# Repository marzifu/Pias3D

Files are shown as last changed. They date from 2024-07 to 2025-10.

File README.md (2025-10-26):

# The Problem
I've always wanted to make and/or source my own Voron and the likes. But the main problem I kept facing is the unimaginably expensive kits that are being sold here in Indonesia, or just the shipment cost + tax that doesn't make sense for me to pay.

Other than that the cost of basically the cheapest CoreXY is around $800 USD _my hopes and dreams_.

# The Solution?
I learnt how to use FreeCAD to draw up my hilariously bad designs until I came to this rendition of the machine which I called Pias. _fancy~_

But no, the name just suggest the eternal loop of fixing, upgrading, maintenance, and what not. Which is what I want to minimize by creating a "proper" machine.

So after scouring countless builds of 3D printers, anything from Rolohaun's build, Mikhail Design's build, and Voron's. I decided to find parts that is easily found here, and thus decided to design a machine around the parts that I find. With the main focus of:

### 1) Keeping It Affordable
The reason this is the main focus is because, good 3D printers are expensive— Even more so for CoreXY systems (Usually an additional $200-$300 _yikes_).

So with that I tried to find hardwares that are a good start, but could be upgraded along the way. Because the important part is for you (and me) as a hobbyist, to be able to build a machine.

### 2) Ease of Procurement
I know this is different to everyone, but my main goal for now is to make a machine that could easily be built by anyone with what we have (Importing's out of the question for us, _unless you have a wae_, in which I dont).

Though there are some Mellow parts that are being sold, the parts are almost 5x of some generic ones. You can get those parts sure, but for the sake of keeping my wallet not empty I am crossing that.

### 3) Upgrade and Update
My first experience with troubleshooting a printer is with a Kingroon KP3S Pro V2, which wasn't fun. I had to replace the mainboard two times, and then ended up switching to a BTT board which is going great.

Tinkering is not fun, if its undocumented and you can reach no one. With that the plan is to document every single upgrades, and update this repository for future builds. It could be some loose fits, or even some arbitrary auxiliary stuff, but documentations are crucial for the longevity of this project.

# Changelogs
### 04/25/2025
Finally back to maintaining this repository after I actually finished the 4th? 6th? rendition of this project. The basic idea of selling it is still in mind, but right not he focus is to have a proper prototype build that could work to print virtually any "normal" material eg. PETG, ABS, ASA, TPU.

I'll try to make a comprehensive build guide, but I do not know how to make a guide like how Voron/Annex which is what I strive for. It's going to be scuffed, but please bear with me.

The next update on this log would probably be an update by creating BOM and pricing in IDR (Indonesian Rupiah), and then converting it to dollars and then saving the links somewhere.
Cheers to this project!

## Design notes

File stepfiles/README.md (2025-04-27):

# A Slight Warning
The designs I have are rough. I have no actual experience in any CAD designs.

I find some parts have a slightly cursed geometry or slices, and that is because that is the only idea I have to actually solve the problem at hand.
Please scrutinize my designs, and help me learn and improve in designing stuff.

Other than that please edit the files to your hearts content :)

# Overview
Attached is a (v1) overview
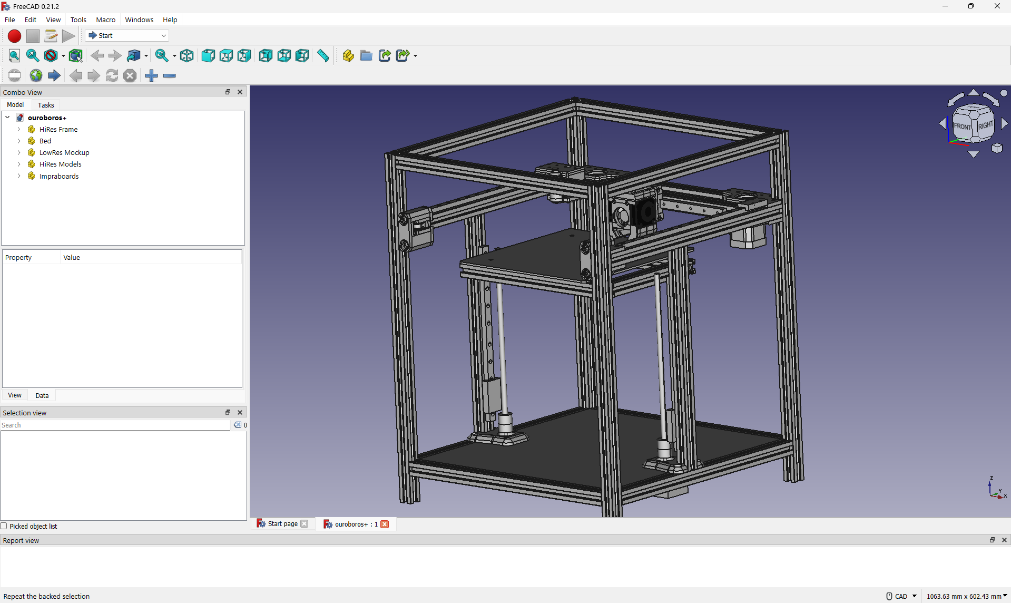
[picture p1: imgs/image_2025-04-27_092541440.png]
Overview


The picture and the 'version' tag will be continously updated with newer versions of the model.

The next goal is to have a rendered version to showcase here with different sections.

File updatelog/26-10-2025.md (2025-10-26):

# Sunday, 26-10-2025
### This log is meant as a way to log the problems that has came up, and my thoughts on the current problems.

Quick update on the current progress

The printer has been built, and is running, though there are some hiccups along the way.
A comprehensive list of BOM could already be made, but I will do that later after a redesign on the current Pias design.

The current plan is to start redesigning starting from the extruder unit, and move to the other parts from there.
I plan to keep the semi-organic-ish design (rarely hard edges), on most of the parts and improve parts that still have a lot of sharp edges.

The thing that I wanted to highlight on this redesign is that in the current rendition of the extruder unit is lackluster.
From the assembly process, and other issues like the management of the GT2 Belt and cables. The process is convoluted, and very tedious to do.
Especially if the goal is to assemble it flush, and close to no wobble.

The glaring issue is that the four contact point of the extruder units is in a weird place, that could be remedied quite easily.

The current plan is to make make the main extruder units (Hotend, Fans, and whatnot) to be separate from the extruder's carriage.
Meaning the main extruder and it's carriage would be separated to two different object if the four contact points were to be taken off.

### What do you even mean by that?

The current main extruder unit is built into three parts, Face, Front, and Back.  

**Face** is the biggest part, including the duct, and the place where the fans will be held.  
**Front** is the first half of the hotend holder, that is closer to the face part.  
**Back** is the second half of the hotend holder, that is closer to the extruder carriage.  

The assembly process for the whole thing is as such:  

1. Prepare the GT2 Belt, and all the cables from the 3 fans, hotend, and klicky.
2. Put the hotend in the Front and Back parts, while managing the belt and cables.
3. Put the assembled FB (Front - Back) unit, and screw the mounting points to the extruder carriage  
   again, mind the cable and belts.
4. If the cable and the belt are managed correctly, the FB unit should be flush with the carriage, if not. Then the belt or cable could be in between.
5. After the FB unit is correctly installed, then continue to prepare the addition of the Face unit.

The list doesn't really do the complexity justice, because the fans has to be placed in advance in the Face unit,
and the cables must have enough slack to not destroy the connection on the fans itself, but not too much so that the fans (especially the part cooling)
would not be tight in the fan places.

All this would make the face part dangle while you have to adjust the position of the GT2 Belt and still having to cable manage so that everything is in the correct place. _yikes_

Then the thought of writing what is wrong with the current edition came up.  
The main thing that I want to fix first is to do separate the two assembly, and then proceed to do a refinement on duct design, and some optimizing on the XY Carriage.

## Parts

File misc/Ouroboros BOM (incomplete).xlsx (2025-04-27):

Category | Item | Details | Quantity | Price | Sub-total | Total
Main Frame | 2020 T Slot | 50cm | 4 | Rp 25000.00 | Rp 100000.00 | Rp 2435810.00
 | 2020 T Slot | 36cm | 10 | Rp 18000.00 | Rp 180000.00
 | 2020 T Slot | 34cm | 1 | Rp 17000.00 | Rp 17000.00
 | 2020 T Slot | 32cm | 2 | Rp 16000.00 | Rp 32000.00
 | 2020 T Slot | 27cm | 2 | Rp 13500.00 | Rp 27000.00
 | 2020 T Slot | 24cm | 1 | Rp 12000.00 | Rp 12000.00
 | 2020 T Slot | 15cm | 2 | Rp 7500.00 | Rp 15000.00
Motion | Nema 17 | Hanpose 17HS4401S | 4 | Rp 95000.00 | Rp 380000.00
 | MGN9H + Rail | 300mm | 2 | Rp 200000.00 | Rp 400000.00
 | MGN12H + Rail | 300mm* | 3 | Rp 200000.00 | Rp 600000.00
 | T8x8 | 250mm | 2 | Rp 39000.00 | Rp 78000.00
 | POM Screw Nut |  | 2 | Rp 20000.00 | Rp 40000.00
 | Rigid Coupler | Generally D20 L25 | 2 | Rp 30000.00 | Rp 60000.00
 | GT2 Belt 6mm | 2 m | 1 | Rp 100000.00 | Rp 100000.00
 | GT2 20T 6W Pulley | 5mm bore | 2 | Rp 10000.00 | Rp 20000.00
 | GT2 20T 6W Toothed Idler | 5mm bore | 2 | Rp 13000.00 | Rp 26000.00
 | GT2 20T 6W Smooth Idler | 5mm bore | 10 | Rp 13000.00 | Rp 130000.00
Fasterner | M6 x 12 BHCS | Frame joints | 30 | Rp 1567.00 | Rp 47010.00
 | M4 x 12 Countersunk | Bed mounting | 4 | Rp 700.00 | Rp 2800.00
 | M5 x 10 BHCS | XYZ part mounting | 50 | Rp 800.00 | Rp 40000.00
 | M3 x 8 BHCS | Rails mounting | 50 | Rp 500.00 | Rp 25000.00
 | M4 Sliding T Nut | Bed mounting | 4 | Rp 1000.00 | Rp 4000.00
 | M3 Sliding T Nut | Rails mounting | 50 | Rp 1000.00 | Rp 50000.00
 | M5 Sliding T Nut | XYZ part mounting | 50 | Rp 1000.00 | Rp 50000.00

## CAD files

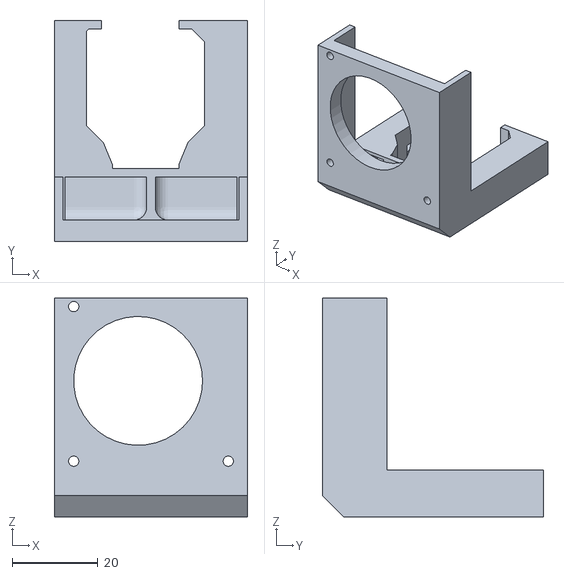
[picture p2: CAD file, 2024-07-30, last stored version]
STL/Part Cooling Duct.stl
45.0 x 51.5 x 51.0

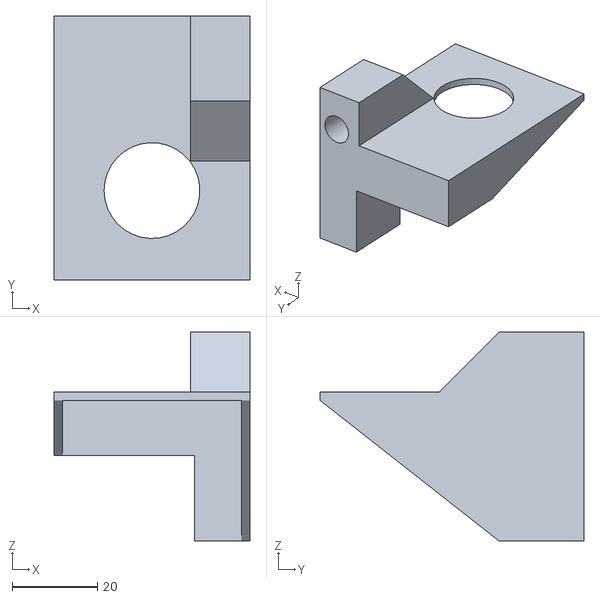
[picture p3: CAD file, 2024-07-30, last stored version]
STL/Right Motor Holder.stl
46.0 x 62.0 x 49.0

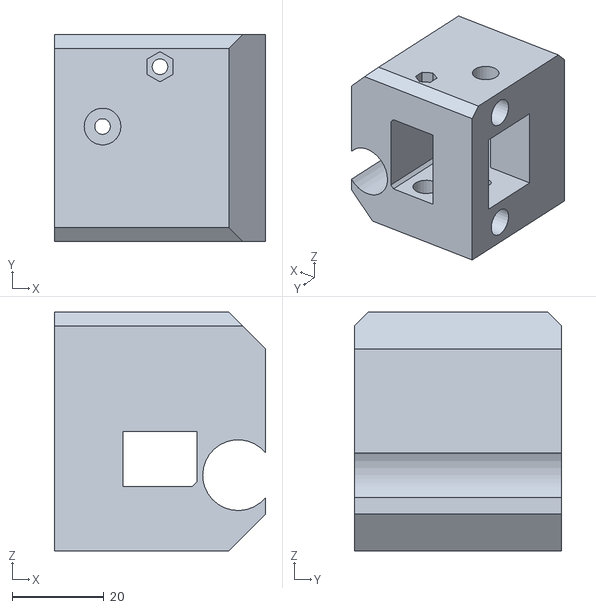
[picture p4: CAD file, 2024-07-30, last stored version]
STL/Right Gantry Holder.stl
46.0 x 45.0 x 52.0

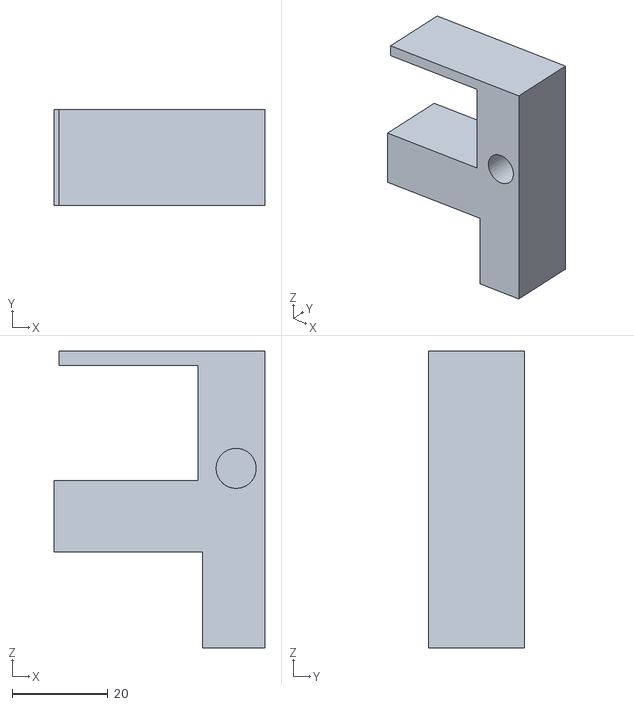
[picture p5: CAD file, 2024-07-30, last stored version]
STL/Right Idler.stl
44.0 x 20.0 x 62.0

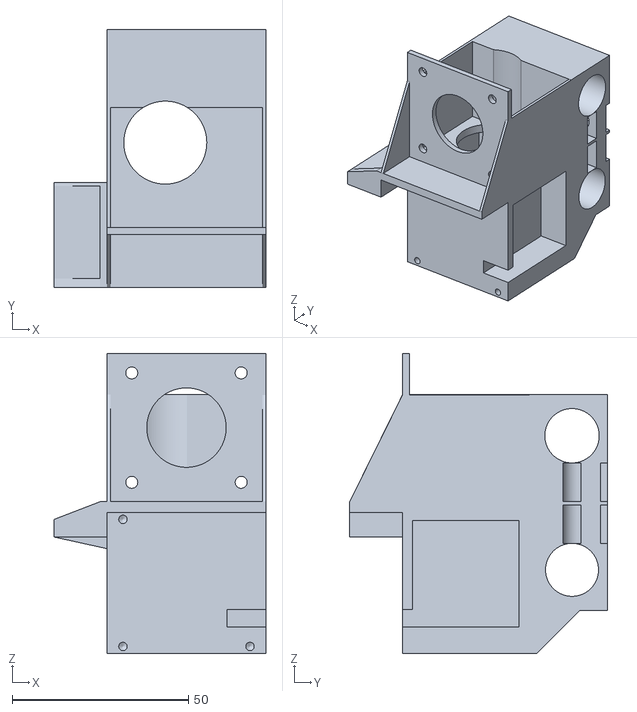
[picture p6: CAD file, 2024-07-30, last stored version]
STL/Carriage.stl
60.0 x 73.0 x 85.0

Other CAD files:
STL/Left Motor Holder.stl
STL/Left Gantry Holder.stl
STL/Left Idler.stl

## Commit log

2024-07-30 Added STL Files
    Unfinished STL Files added
    -> Carriage needed 3D Touch Holder
    -> Idler needed Holes and unfinished construction
    -> Motor holder needed bolt holes
    [Carriage.stl, Left Gantry Holder.stl, Left Idler.stl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]
2025-04-24 Delete STL directory
    Deleting old STL files. Severely deprecated.
    [Carriage.stl, Left Gantry Holder.stl, Left Idler.stl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]
2025-04-27 added unfinished BOM
    tap and drill came in, so I am working on the frame~
    [Ouroboros BOM (incomplete).xlsx]
2025-04-27 reuploading BOM to misc
    keeping it tidy~
    [Ouroboros BOM (incomplete).xlsx]
2025-04-27 added unfinished BOM
    tap and screw came in, so I am drilling and tapping first!
    [Ouroboros BOM (incomplete).xlsx]
2025-10-26 Update log for redesign thoughts on extruder unit
    Expanded update log with detailed thoughts on redesigning the extruder unit and assembly process.
